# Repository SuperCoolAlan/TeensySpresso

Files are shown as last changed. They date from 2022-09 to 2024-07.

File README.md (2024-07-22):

# TeensySpresso :coffee:
Teensy 3.2 PID controller, PCB, and enclosure design for a single-boiler Rancilio Silvia espresso machine.

## :robot:
All of the existing Open Source solutions for an integrated PID controller were too big to fit in my single-boiler Rancilio Silvia v2. I put this together and glued it on above the steam wand's valve. I didn't want to change the look or feel of the machine at all, so I have not included a physical display in the design. Instead, a web-UI will be hosted from the ATWINC1500.
The heating element's control circuit bypasses the OEM brew thermistor which leaves the steam and safety circuits intact.

## TODO
- [x] Install and test
- [x] LED pad spacing
- [x] Relay footprint
- [x] Update schematic to connect WINC_EN to a pin... oops
- [x] Enable WINC1500 WiFi module :signal_strength:
  - [x] Host WiFi from module, enable incoming connections
  - [x] Update firmware to 19.6.1 by creating new BSP for teensy or using supported board. My firmware version is 19.4.4
- [x] Assemble print of v2
- [ ] MQTT
  - [x] deploy MQTT broker to cloud
  - [x] MQTT client in Teensy connects to MQTT broker in cloud
  - [ ] allow use of WiFi and Temp Sensors via SPI by using CS lock
  - [x] access MQTT broker by domain rather than IP
- [ ] Host Web-UI for monitoring and control :chart:
  - [ ] Host Next.js app on (Vercel?)
  - [ ] Monitor w/ charts
  - [ ] Configurable temperature setpoint
  - [ ] Configurable mode (brew temp, steam temp)
- [ ] Docs :scroll:
  - [x] Circuit diagram
  - [ ] Pics
  - [x] BOM
- [ ] Results

##
Enjoy the brew. Cheers to productivity!
:coffee:

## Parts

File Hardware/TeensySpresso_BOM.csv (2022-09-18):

Mouser #: | Mfr. #: | Desc.: | Order Qty. | Notes
490-PSK-15D-5 | PSK-15D-5 | AC/DC Power Modules AC/DC Power Modules ac-dc, 15 W, 5 Vdc, single output, encapsulated PCB, 85~305 Vac | 1
710-691111710002 | 691111710002 | Pluggable Terminal Blocks Pluggable Terminal Blocks WR-TBL 250VAC 15A 2P Straight | 2
225-RP1A23D10 | RP1A23D10 | Solid State Relays - PCB Mount Solid State Relays - PCB Mount SSR ZS PCB MT W/H.S. 230V 10A | 1
743-HV-5RGB60 | HV-5RGB60 | Standard LEDs - Through Hole Standard LEDs - Through Hole RGB LED | 2
280-CR5-220-RC | 280-CR5-220-RC | Wirewound Resistors - Through Hole Wirewound Resistors - Through Hole 220ohms 5% Tol | 2
 |  | Teensy 3.2 | 1
 |  | Adafruit MAX31855 breakout board | 1
 |  | Adafruit WINC1500 breakout board | 1
 |  | M5-0.8 x 10mm screws | 3 | Ace Hardware
 | https://www.amazon.com/dp/B08P1TNNR6/ref=cm_sw_r_apa_i_5QH34E6J1E39QVHMM07F_0 | M5-0.8 brass threaded inserts | 3 | Dimensions LxWxH | 0.37 x 0.26 x 0.26 inches

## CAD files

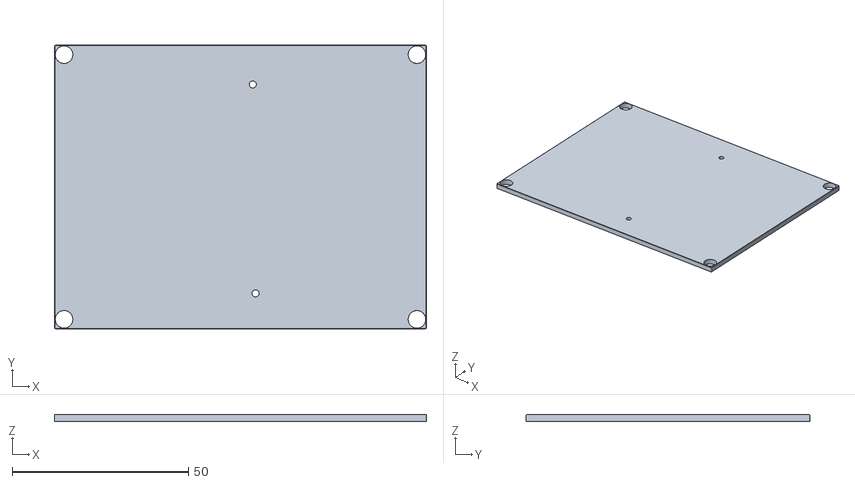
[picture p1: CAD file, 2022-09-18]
Hardware/220918_TeensySpresso_EnclosureLid_v1.stl
105.4 x 80.4 x 2.00

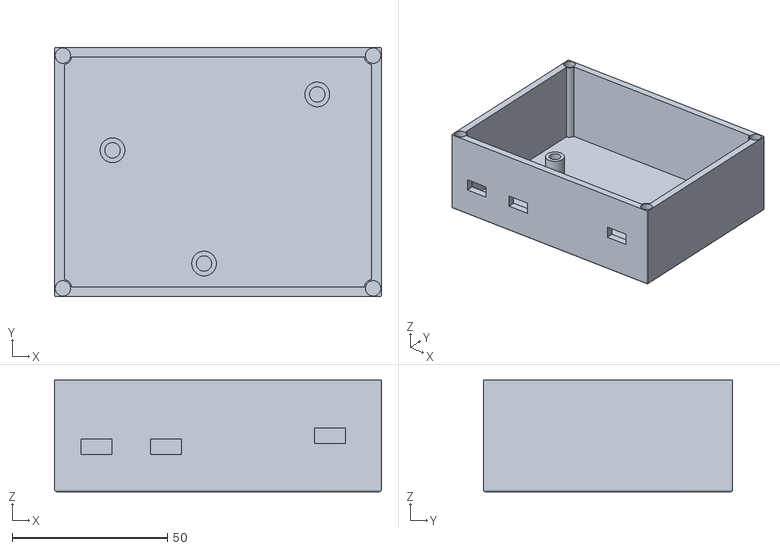
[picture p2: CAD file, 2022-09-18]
Hardware/220918_TeensySpresso_EnclosureBase_v1.stl
105.4 x 80.4 x 36.0

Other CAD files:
Hardware/220717_EspressoControllerSchematicv1 v48.f3z

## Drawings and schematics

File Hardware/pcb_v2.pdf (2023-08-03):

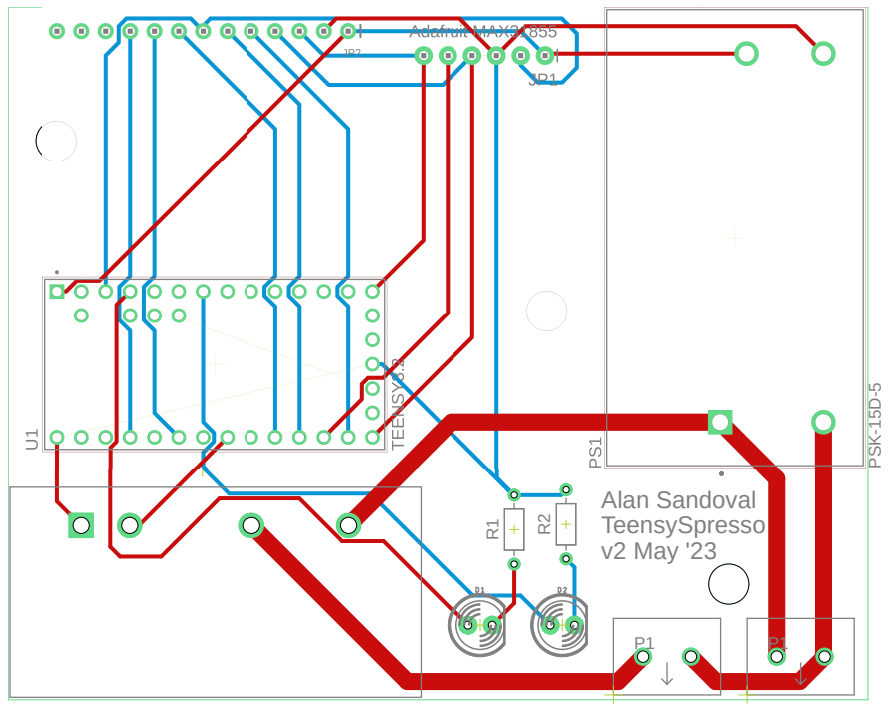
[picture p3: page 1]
Alan Sandoval TeensySpresso; v2 May '23 R¹; PSK⁻¹⁵D⁻⁵

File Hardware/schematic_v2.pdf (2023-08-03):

A

A

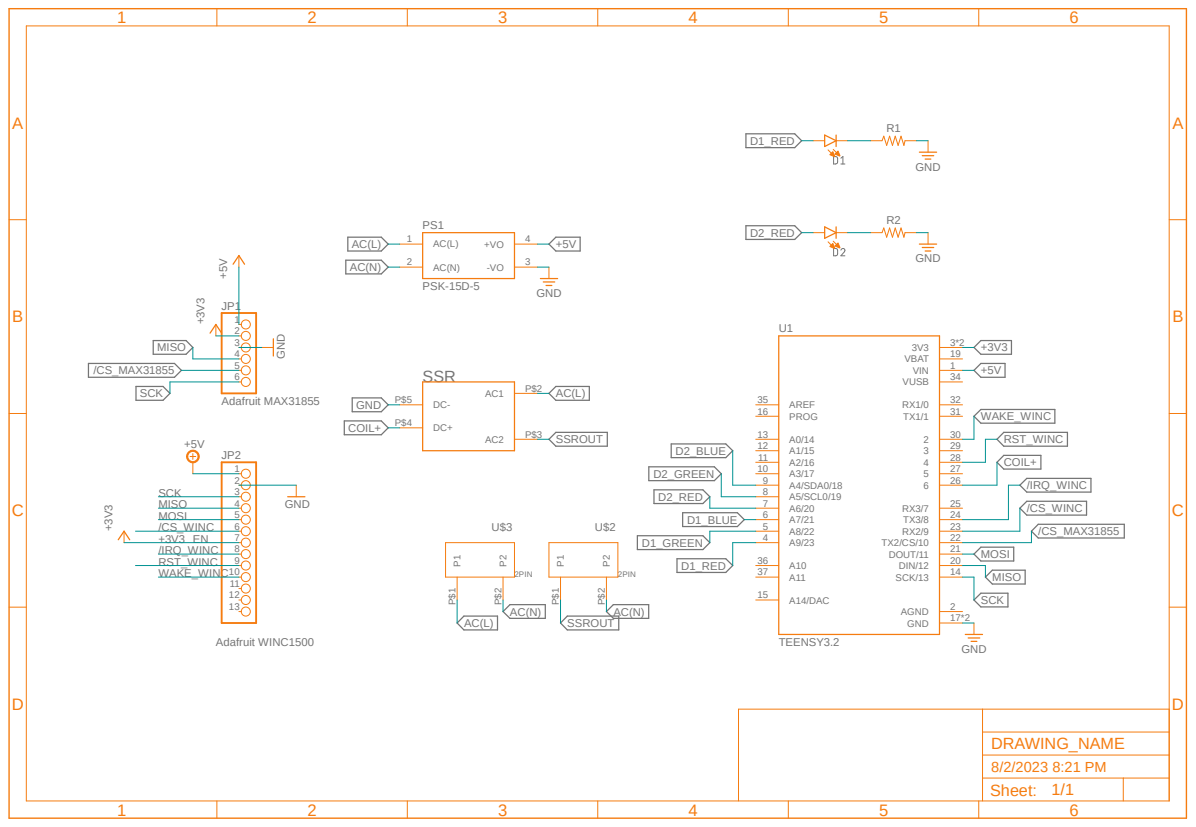
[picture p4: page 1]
Adafruit WINC1500; TEENSY3.2; PSK-15D-5; GND; GND GND ⁺³V³; Adafruit MAX31855 ⁺⁵V; GND +3V³; SSR; VBAT; VIN; AGND; A0/14 13 A1/15 12 A2/16 11 A3/17 10 A4/SDA0/18 9 A5/SCL0/19 8 A6/20 7 A7/21 6 A8/22 5; DOUT/11; DIN/12; SCK/13; A14/DAC 15; AREF 35; VUSB; PROG 16; 2PIN; /IRQ_WINC; MISO; /CS_WINC; RST_WINC; WAKE_WINC; COIL+; SSROUT; D1_RED; D1_GREEN; D1_BLUE; D2_RED; D2_GREEN; D2_BLUE; SCK; /CS_MAX31855; MOSI; DRAWING_NAME; 8/2/2023 8:21 PM Sheet: 1/1

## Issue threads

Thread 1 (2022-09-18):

WINC_EN does not connect to the Teensy32

SuperCoolAlan, 2022-09-18:
I had to tie 3.3VDC to EN to make it work. Address this in the schematic, PCB design, and documentation

SuperCoolAlan, 2022-09-18:
💩

SuperCoolAlan, 2023-05-09:
Fixed by https://github.com/SuperCoolAlan/TeensySpresso/pull/2

Closed 2023-05-09.

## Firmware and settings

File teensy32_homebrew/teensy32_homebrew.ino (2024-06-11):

// Rancilio Silvia PID controller
// Alan Sandoval
// June 2024

#include <SPI.h>
#include <WiFi101.h>
#include "Adafruit_MAX31855.h"
#include <PID_v1_bc.h>
#include "TeensyThreads.h"
#include <MQTT.h>

#define CS 10
#define SCLK 13
#define DIN 12

#define RelayPin 6
#define RedLEDOne 20 // bright light shows when PID output is on
#define RedLEDTwo 23 // status for system (solid lit while starting, blinking while running)

unsigned long blinkPreviousMillis = 0;  // will store last time LED was updated
const long blinkInterval = 1000;  // interval at which to blink (milliseconds)

#include "arduino_secrets.h" 
///////please enter your sensitive data in the Secret tab/arduino_secrets.h
char ssid[] = SECRET_SSID;        // your network SSID (name)
char pass[] = SECRET_PASS;    // your network password (use for WPA, or use as key for WEP)
int keyIndex = 0;                 // your network key Index number (needed only for WEP)
int status = WL_IDLE_STATUS;
#define WINC_CS 9
#define WINC_IRQ 8
#define WINC_RST 4
#define WINC_EN -1


WiFiClient net;
MQTTClient client;
unsigned long mqttLastMillis = 0;

// Connect to Temperature Module
Adafruit_MAX31855 tc0(SCLK, CS, DIN);
double latestTemp;

//Define PID vars
double Setpoint, Input, Output;
int WindowSize = 1000;
unsigned long windowStartTime;

//Specify the links and initial tuning parameters
PID myPID(&Input, &Output, &Setpoint, 1, 1, 1, DIRECT);

void setup() {
  // create serial
  Serial.begin(9600);
  long unsigned debug_start = millis ();
  while (!Serial && ((millis () - debug_start) <= 2000)); 

  // configure SPI outputs
  pinMode(CS, OUTPUT);
  digitalWrite(CS, HIGH);
  pinMode(RedLEDTwo, OUTPUT);
  digitalWrite(RedLEDTwo, HIGH);

  setupPid();
  // Setting pins
  setupWiFi();
  if ( status == WL_CONNECTED ) {
    Serial.println("WiFi connection successful... attempting to connect to MQTT");
    // threads.addThread(connectMqtt);
    connectMqtt();
  }

  // threads.addThread(queryTemp);
  // threads.addThread(calculatePid);
}

void loop() {
  blink();

  // publish a message roughly every second.
  if (millis() - mqttLastMillis > 1000) {
    mqttLastMillis = millis();
    client.publish("/teensyspresso", "ilikebeef");
  }
}

void queryTemp() {
  while(1) {
    digitalWrite(CS, LOW);
    latestTemp = tc0.readCelsius();
    digitalWrite(CS, HIGH);
    Serial.println(latestTemp);
    threads.delay(WindowSize / 2);
  }
}

void blink() {
  unsigned long currentMillis = millis();
  if (currentMillis - blinkPreviousMillis >= blinkInterval) {
    // save the last time you blinked the LED
    blinkPreviousMillis = currentMillis;

    // set the LED with the ledState of the variable:
    digitalWrite(RedLEDTwo, !digitalRead(RedLEDTwo));
  }
}

//
// PID functions
//

void setupPid() {
    pinMode(RelayPin, OUTPUT);
    pinMode(RedLEDOne, OUTPUT);
    
    windowStartTime = millis();
  
    //initialize the pid variables we're linked to
    Setpoint = 100;
    Input = 0;
  
    //tell the PID to range between 0 and the full window size
    myPID.SetOutputLimits(0, WindowSize);
  
    //turn the PID on
    myPID.SetMode(AUTOMATIC);
}

void calculatePid() {
  while(1) {
    // Serial.println("running calculatePid()");
    if(isnan(latestTemp)) {
      Serial.print("MAX31855 error: ");
      Serial.println(tc0.readError());
    } else{
      // Serial.print("temp: "); 
      // Serial.println(latestTemp);
      
      myPID.Compute();

      unsigned long now = millis();
      if (now - windowStartTime > WindowSize) { //time to shift the Relay Window
        windowStartTime += WindowSize;
      }
      if (Output > now - windowStartTime) {
        digitalWrite(RelayPin, HIGH);
        digitalWrite(RedLEDOne, HIGH);
      }
      else {
        digitalWrite(RelayPin, LOW);
        digitalWrite(RedLEDOne, LOW);
      }
      // Serial.print("Relay: ");
      // Serial.println(digitalRead(RelayPin));
    }
    threads.delay(WindowSize / 2);
  }
}

//
// MQTT
//

// void setupMqtt() {

// }

void connectMqtt() {
  Serial.print("subscribing to MQTT server...");
  while (WiFi.status() != WL_CONNECTED) {
    Serial.print("WiFi did not stabilize.");
    threads.delay(1000);
  }

  // Note: Local domain names (e.g. "Computer.local" on OSX) are not supported
  // by Arduino. You need to set the IP address directly.
  client.begin("3.13.75.214", net); //teensyspresso.asandov.com
  client.onMessage(mqttMessageReceived);

    while (!client.connect("teensyspresso")) {
      Serial.print("\n(re)connecting to MQTT...");
      Serial.print(".");
      threads.delay(500);
    }

    Serial.println("\nconnected!");

    client.subscribe("/teensyspresso");
    threads.delay (5000);
    client.unsubscribe("/teensyspresso");
}

void mqttMessageReceived(String &topic, String &payload) {
  Serial.println("incoming: " + topic + " - " + payload);

  // Note: Do not use the client in the callback to publish, subscribe or
  // unsubscribe as it may cause deadlocks when other things arrive while
  // sending and receiving acknowledgments. Instead, change a global variable,
  // or push to a queue and handle it in the loop after calling `client.loop()`.
}

//
// WiFi Functions
//

void setupWiFi() {
  WiFi.setPins(WINC_CS, WINC_IRQ, WINC_RST, WINC_EN);

  // check for the presence of the shield:
  if (WiFi.status() == WL_NO_SHIELD) {
    Serial.println("WiFi shield not present");
    // don't continue
    while (true);
  }

  // attempt to connect to WiFi network:
  int count = 0;
  while ( status != WL_CONNECTED && count < 5 ) {
    count++;
    Serial.print(String("Attempt number ") + count + String(" of 5 to connect to Network named: "));
    Serial.println(ssid);                   // print the network name (SSID);
    // Connect to WPA/WPA2 network. Change this line if using open or WEP network:
    status = WiFi.begin(ssid, pass);
    // wait 7 seconds for connection:
    threads.delay(7000);
  }
  if ( status != WL_CONNECTED ) {
    Serial.println("Failed to connect to WiFi!");
  } else {
    // you're connected now, so print out the status
    printWiFiStatus();
  }
}

void printWiFiStatus() {
  // print the SSID of the network you're attached to:
  Serial.print("SSID: ");
  Serial.println(WiFi.SSID());

  // print your WiFi shield's IP address:
  IPAddress ip = WiFi.localIP();

  Serial.print("IP Address: ");
  Serial.println(ip);

  // print the received signal strength:
  long rssi = WiFi.RSSI();
  Serial.print("signal strength (RSSI):");
  Serial.print(rssi);
  Serial.println(" dBm");
}

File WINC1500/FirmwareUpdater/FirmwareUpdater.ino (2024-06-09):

/*
  FirmwareUpdate.h - Firmware Updater for WiFi101 / WINC1500.
  Copyright (c) 2015 Arduino LLC.  All right reserved.

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
  You should have received a copy of the GNU Lesser General Public
  License along with this library; if not, write to the Free Software
  Foundation, Inc., 51 Franklin St, Fifth Floor, Boston, MA  02110-1301  USA
*/

#include <WiFi101.h>
#include <spi_flash/include/spi_flash.h>

#define WINC_CS 9
#define WINC_IRQ 8
#define WINC_RST 4
#define WINC_EN -1

#define WINC1501_RESET_PIN 4
#define WINC1501_INTN_PIN 8
#define WINC1501_SPI_CS_PIN 9

typedef struct __attribute__((__packed__)) {
  uint8_t command;
  uint32_t address;
  uint32_t arg1;
  uint16_t payloadLength;

  // payloadLenght bytes of data follows...
} UartPacket;

static const int MAX_PAYLOAD_SIZE = 1024;

#define CMD_READ_FLASH        0x01
#define CMD_WRITE_FLASH       0x02
#define CMD_ERASE_FLASH       0x03
#define CMD_MAX_PAYLOAD_SIZE  0x50
#define CMD_HELLO             0x99

void setup() {
  Serial.begin(9600);
  while (!Serial) {
    ; // wait for serial port to connect. Needed for native USB port only
  }
  Serial.println(F("Updating WINC1500 Firmware"));

  // Setting pins
  WiFi.setPins(WINC_CS, WINC_IRQ, WINC_RST, WINC_EN);

  nm_bsp_init();
  Serial.println(F("Initialized nm_bsp"));
  if (m2m_wifi_download_mode() != M2M_SUCCESS) {
    Serial.println(F("Failed to put the WiFi module in download mode"));
    while (true)
      ;
  }
}

void receivePacket(UartPacket *pkt, uint8_t *payload) {
  // Read command
  uint8_t *p = reinterpret_cast<uint8_t *>(pkt);
  uint16_t l = sizeof(UartPacket);
  while (l > 0) {
    int c = Serial.read();
    if (c == -1)
      continue;
    *p++ = c;
    l--;
  }

  // Convert parameters from network byte order to cpu byte order
  pkt->address = fromNetwork32(pkt->address);
  pkt->arg1 = fromNetwork32(pkt->arg1);
  pkt->payloadLength = fromNetwork16(pkt->payloadLength);

  // Read payload
  l = pkt->payloadLength;
  while (l > 0) {
    int c = Serial.read();
    if (c == -1)
      continue;
    *payload++ = c;
    l--;
  }
}

// Allocated statically so the compiler can tell us
// about the amount of used RAM
static UartPacket pkt;
static uint8_t payload[MAX_PAYLOAD_SIZE];

void loop() {
  receivePacket(&pkt, payload);

  if (pkt.command == CMD_HELLO) {
    if (pkt.address == 0x11223344 && pkt.arg1 == 0x55667788)
      Serial.print("v10000");
  }

  if (pkt.command == CMD_MAX_PAYLOAD_SIZE) {
    uint16_t res = toNetwork16(MAX_PAYLOAD_SIZE);
    Serial.write(reinterpret_cast<uint8_t *>(&res), sizeof(res));
  }

  if (pkt.command == CMD_READ_FLASH) {
    uint32_t address = pkt.address;
    uint32_t len = pkt.arg1;
    if (spi_flash_read(payload, address, len) != M2M_SUCCESS) {
      Serial.println("ER");
    } else {
      Serial.write(payload, len);
      Serial.print("OK");
    }
  }

  if (pkt.command == CMD_WRITE_FLASH) {
    uint32_t address = pkt.address;
    uint32_t len = pkt.payloadLength;
    if (spi_flash_write(payload, address, len) != M2M_SUCCESS) {
      Serial.print("ER");
    } else {
      Serial.print("OK");
    }
  }

  if (pkt.command == CMD_ERASE_FLASH) {
    uint32_t address = pkt.address;
    uint32_t len = pkt.arg1;
    if (spi_flash_erase(address, len) != M2M_SUCCESS) {
      Serial.print("ER");
    } else {
      Serial.print("OK");
    }
  }
}

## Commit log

2022-09-18 Upload enclosure stl v1
    A nice box? Probably will not be perfect, but it may do!
    [220918_TeensySpresso_EnclosureBase_v1.stl, 220918_TeensySpresso_EnclosureLid_v1.stl]
2022-09-18 Delete TeensySpresso_BOM.xls
    wrong ugly format
    [TeensySpresso_BOM.xls]
2022-09-18 BOM correct format
    [TeensySpresso_BOM.csv]
2024-06-09 mutually exclusive web server and pid
2024-06-11 wip multiplex spi
